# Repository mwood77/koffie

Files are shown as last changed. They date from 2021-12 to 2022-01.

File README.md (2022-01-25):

# Koffie ☕
Koffie is an open source project which allows you to programatically set and adjust the boiler pressure of your espresso machine in real time.

Too much reading? [Watch an overview of the device here!](https://www.youtube.com/watch?v=FLI8BKzOYMY)

### Current development (features requests and bugs)
You can find the task board here, which shows work in progress: 
- [View our project board](https://github.com/mwood77/koffie/projects/1)

### Found a bug?
- [Report it here - please make sure to include the what & how](https://github.com/mwood77/koffie/issues/new)

### Want to contribute? Great!
- Fork it and create a PR!

## Read first!
- This proceedure is 100% reversible
- There are some passive safety limitations built into the software, which include:
    - You have a maximum boiler pressure of 1.4 BAR
- This project was designed/developed on a pre-millenium La Pavoni Europiccola (double rocker; power switch + hi/low)
    - Your implementation may be different than what's documented here, but with some simple probing of your espresso machine circuitry, you should be able to implement this easily.

# User guide
> By default, koffie boots into espresso mode

## Automatic Mode
- Tap either button to toggle between programming modes:
    - Espresso (low pressure)
    - Milk (high pressure)
- The screen will update to show you what mode you're currently in, in addition to the LEDs (if equipped).

## Manual Mode
- Turning the rotary encoder (knob) will toggle Koffie into Manual mode.
    - The pressure readout will show a **Target (TARG:)** and **Actual (ACTL:)** values. 
    - Turning the encoder will either increase or decrease the **target value**. Koffie will then take action to intercept the target value.
- The screen will update to show you what mode you're currently in, in addition to the LEDs (if equipped).

## Programming Mode
In addition to Automatic and Manual operation, you may also overwrite the default pressure values in Koffie's memory. Do set custom values do the following:
1. Turn on Koffie (your espresso machine does not need to be on).
1. Turn the encoder to swtich into **Manual Mode**
1. Set the **Target (TARG:)** to your desired pressure level.
1. Press and hold either button until the LED flashes (approx. 2 seconds)
    - Your new value is now stored in memory.
1. Tap the same button to go back to automatic mode and check that value on screen is the value you saved. If not, repeat the steps above.

# Build and install your own Koffie
This section has been split across multiple pages to make the project easier to digest.
1. [Design document](docs/design.md) **<- START HERE**
1. [Parts list and costs](docs/requirements.md)
1. [Circuit diagrams](docs/circuits.md)
1. [Code Configurables](docs/code_configurables.md) **<- READ THIS BEFORE UPLOADING THE CODE TO YOUR ARDUINO**

### Installation (Machine specific)
- La Pavoni
    1. [Europiccola](docs/machines/europiccola.md)

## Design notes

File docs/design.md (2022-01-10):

> [Back to main page](../README.md)

# Design document
The purpose of this document is:
- To outline what functionality the PID, "koffie," has
- How "koffie" behaves when iteracted with by a human
- How "koffie" interacts with an espresso machine

## Program modes
1. Espresso - low pressure for extracting espresso
1. Milk - high pressure for frothing milk
1. Manual - "on the fly" pressure adjustment
1. Programming - overwrite the default pressure levels with custom values

## Controls
- 2 momentary buttons which are used to set and access stored values
    - Button 1:
        - **Momentary press:**
            1. deactivate current program
            1. activate "Espresso Mode" & call-up pressure for extracting espresso
        - **Long press:**
            - See [Progamming Mode](../README.md#programming-mode)
    - Button 2:
        - **Momentary press:** 
            1. deactivate current program
            1. activate "Milk Mode" & call-up pressure for frothing milk
        - **Long press:**
            - See [Progamming Mode](../README.md#programming-mode)
- 1 multi-function rotary encoder
    - If in Espresso or Milk modes:
        - deactivate current program
        - activate "Manual Mode," and enable on-the-fly boiler pressure adjustment
    
## GUI
### Block diagram of interface

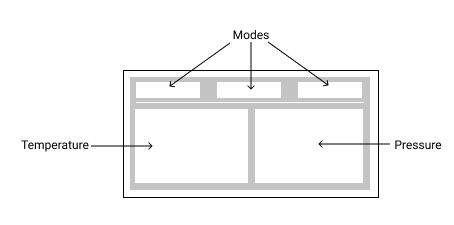
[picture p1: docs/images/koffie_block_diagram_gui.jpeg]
Block diagram of koffie interface


### Populated block diagram interface
|  |  |
| - | - |
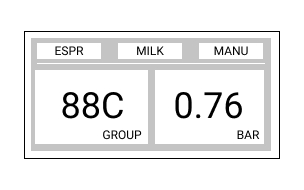
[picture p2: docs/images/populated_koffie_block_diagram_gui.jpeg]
Block diagram of koffie interface
|  | - A single mode is illuminated when activated <br/> - When in "programming mode," the corresponding parent mode will flash <br/> - Temperatures are displayed, if available <br/> - if no probe is connected, `N/C` is displayed |

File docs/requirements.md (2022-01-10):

> [Back to main page](../README.md)

# Parts list and costs

## How much will this cost?
That's hard to answer, but if you purchase everything in the list beneath, it should come to no more than **$60 USD / €53**. 

## Things I've assumed you already know and own
- A "dumb" espresso machine
- A computer
    - The tutorial is written using a Mac, but a Windows or Linux computer is also fine. The instructions should be interchangable.
- A spare phone charger & USB cable to power the Arduino
- How to use a multimeter
- How to solder and de-solder
- Some spare small-gauge wire
- Rudimentary knowledge of electronics
- Some understanding of code (C++) and/or how to use an Arduino
    - However if you follow the instruction to the letter, you should be able to get by without any previous experience.

## Required parts
> You requirements may differ, so this list may or may not be complete depending on what sensors you want to install / your espresso machine.

I've provided links to the parts where I can. Most are sourced from Aliexpress as that's usually the most cost effective option.

#### La Pavoni Europiccola & Professional
- [ ] [Arduino Nano or other compatible](https://aliexpress.com/item/4000903444456.html). 
    - I chose the option: `Type-C USB`
        - If you choose `Type-C USB` be careful of the driver requirements (plug and play on Mac and Linux. Windows, not guaranteed). **If you don't know what this means, select a mico-USB one instead.**
- [ ] [Arduino expansion board](https://s.click.aliexpress.com/e/_9RjuPG).
    - **This is optional**, but it reduces your soldering workload / allows you to wire in new sensors quickly.
- [ ] [A solid state relay](https://s.click.aliexpress.com/e/_9h01hI). 
    - Select the `SSR-40 DA` option, **or make sure you choose a solid state relay that can handle roughly 40A and mains voltage (100-240V).**
- [ ] [An OLED screen](https://nl.aliexpress.com/item/32957309383.html). 
    - An OLED screen has a very wide viewing angle, is high contrast, and is not complex to implement.
- [ ] [An encoder](https://s.click.aliexpress.com/e/_AZFjme). 
- [ ] [A knob for the encoder](https://s.click.aliexpress.com/e/_Atgtlq). 
    - The better the knob, the better the encoder will feel!
- [ ] [2x illuminated momentary switches](https://s.click.aliexpress.com/e/_AFDd3K). 
    - We will be using them to quick-select different memory modes ("Brew mode" & "Frothing mode").
        - Select: 
            - Color: `16 Ring LED`
            - Voltage: `3-6V`
            - Size: `Self-reset momentary`
            - Standard: `choose whatever LED colour you'd like. I'd recommend matching it to your OLED.`
            - Quantity: `2`
- [ ] [An enclosure to mount the electronics](https://s.click.aliexpress.com/e/_AKRz3E).
- [ ] [2x TMP36 analog temperature sensors](https://s.click.aliexpress.com/e/_AWMTHm).
    - We'll hack this to fit in the joint between the group head and boiler.
- [ ] [2x 4k7 resistors (also known as 4700 ohms or 4.7K resistors)](https://www.google.com/search?q=4k7+resistor).
    - We'll use these on our switch's LEDs.
- [ ] [2x A pressure transducer with a minimum rating of 30 PSI / 2 BAR.](https://s.click.aliexpress.com/e/_ALg5YG). 
    - I use 60PSI sensors in this project, but you can change this variable in the project code.
    - I'd recommend you buy 2 examples as these have a habit of failing.
    - This one is great, as the thread size (1/8 NPT) is compatible with the Europiccola's manometer adapter (the gauge adapter that screws atop the sight glass).
    - If you don't have an existing pressure gauge, or need an adapter for this project:
        - [M12 to 1/8 NPT adapter](https://www.google.com/search?q=europiccola+m12+to+1%2F8+npt)
        - [M11 to 1/8 NPT adapter](https://www.google.com/search?q=europiccola+m11+to+1%2F8+npt)
        - If you don't know what size to buy, remove the "big screw" on top of the sight glass and measure the diameter of the threads.
            - 11mm = M11 
            - 12mm = M12

### Optional Extras
- [ ] [Kapton Tape](https://www.google.com/search?q=kpaton+tape).
    - We'll use this to attach our sensors to the coffee machine (this is heat resistant tape).
- [ ] If you have access to a 3D printer, you can print off a faceplate for the enclosure I've linked above.
    - [Find the models here](https://github.com/mwood77/koffie/tree/main/models)

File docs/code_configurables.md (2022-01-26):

> [Back to main page](../README.md)

# Code configurables

## Prerequisites
If you've never used/programmed an Arduino before, I'd strongly suggest you start here:
1. [Arduino - Getting Started](https://www.arduino.cc/en/Guide)
1. [Arduino Nano Quickstart](https://docs.arduino.cc/hardware/nano)

There are a number of files but there are only a few things you **might** need to change. 
You can find these configurable values located between the following headers in `koffie.ino`

<hr>
Please read the comments closesly and do not change any of the other code unless you understand what is going on. If you can see an improvement point, please raise a PR!
<hr>

```
 File: ~/koffie/koffie.ino

// *************************************************************************************
// ****************************** BEGIN CONFIGURABLES **********************************
// *************************************************************************************
 
...
...
...

// *************************************************************************************
// ******************************* END CONFIGURABLES ***********************************
// *************************************************************************************
```

## Arduino Libraries Required
Most of the required libraries are included, or are automatically downloaded on the first compilation.

If the Arduino IDE (2.0) fails to compile the code, it's probably unable to find a library. Please make sure you've downloaded the following (slightly obscure) libraries:

1. **Encoder** - by Paul Stoffregen
    - Version 1.4.2
1. **OneButton** - by Matthias Hertel
    - Version 2.0.4
1. **Adafruit SSD1306** - by Adafruit
    - Version 2.5.1
    - Make sure to install all of the required dependencies

## Helpful hints
1. Make sure to turn on the option `Show verbose output during: [x] compile`
    - This is found under **Arduino IDE** -> **Preferences** on macOS
    - This is found under **File** -> **Preferences** on Windows
    - This will give a lot of output during compile, but it makes it much easier to diagnose what went wrong.

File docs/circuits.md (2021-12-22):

> [Back to main page](../README.md)

# Circuit diagrams

## Arduino
You can view an online version of the circuit diagram here:
- [Koffie - arduino wiring diagram](https://crcit.net/c/60b06504545248359b3b8e42acd408be)

Alternatively, you can view a visual representation of the wiring on the emulated version of this project:
 - [Koffie - running in an arduino simulator](https://wokwi.com/arduino/projects/316601625012601409)

### Circuit Diagram
wiring diagram for koffie

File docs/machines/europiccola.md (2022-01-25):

> [Back to main page](../../README.md)

# Europiccola

## Wiring
- Wire the relay's switched voltage (mains) between the thermocouple (thermal fuse) and the power switch.
- If your machine does not have a thermocouple, wire the relay between the switch.

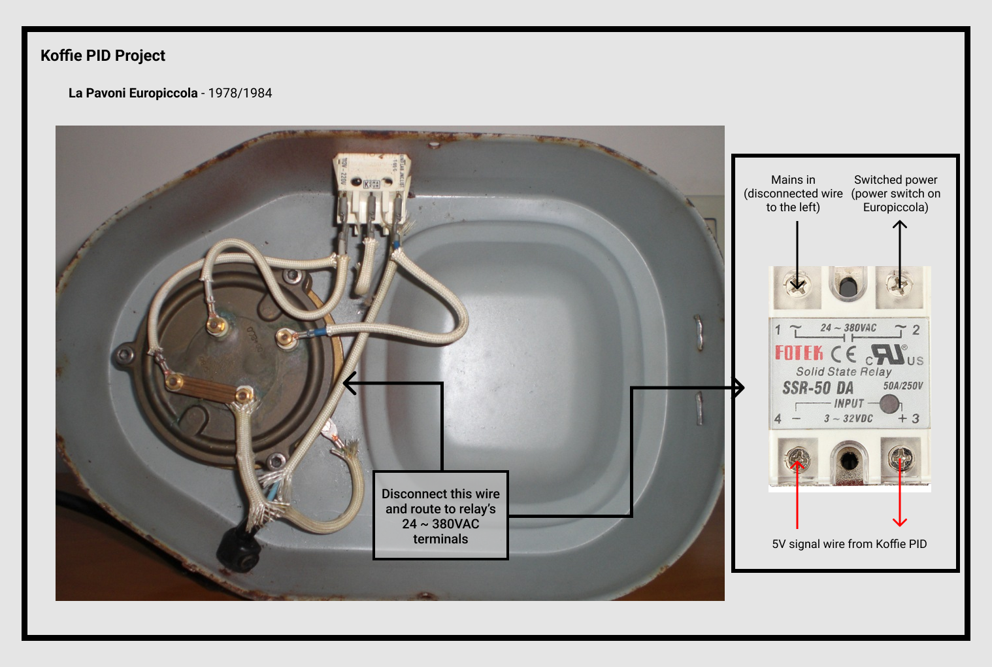
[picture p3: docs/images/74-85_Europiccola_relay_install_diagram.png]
image of europiccola ball bearing pressure safety valve
    
    - **Image Credit**: 
        - Francesco Ceccarelli
        - [La Pavoni - wiring diagrams](http://www.francescoceccarelli.eu/lapavoni_schemi_eng.htm)

## Modifying the pressure
> ⚠️ This is exceptionally dangerous! Only do so at your own risk! ⚠️

### Mechanical Pressure Valve
Should you want more pressure from your boiler, do the following:
- Dissasemble the mechanical pressure valve and slightly pull on the spring. By stretching it out, you increase the pressure placed on the ball bearing, which will increase the amount of pressure required to actuate the valve. This increases the overall boiler pressure.
- Make small adjustments, then bring the machine up to temperature and check at what pressure the valve opens. Re-adjust as necessary.
- **DO NOT TAKE THE PRESSURE ABOVE 1.5 BAR!** That is unsafe, and there is no need to brew espesso/froth milk at pressures above 1.3 BAR.
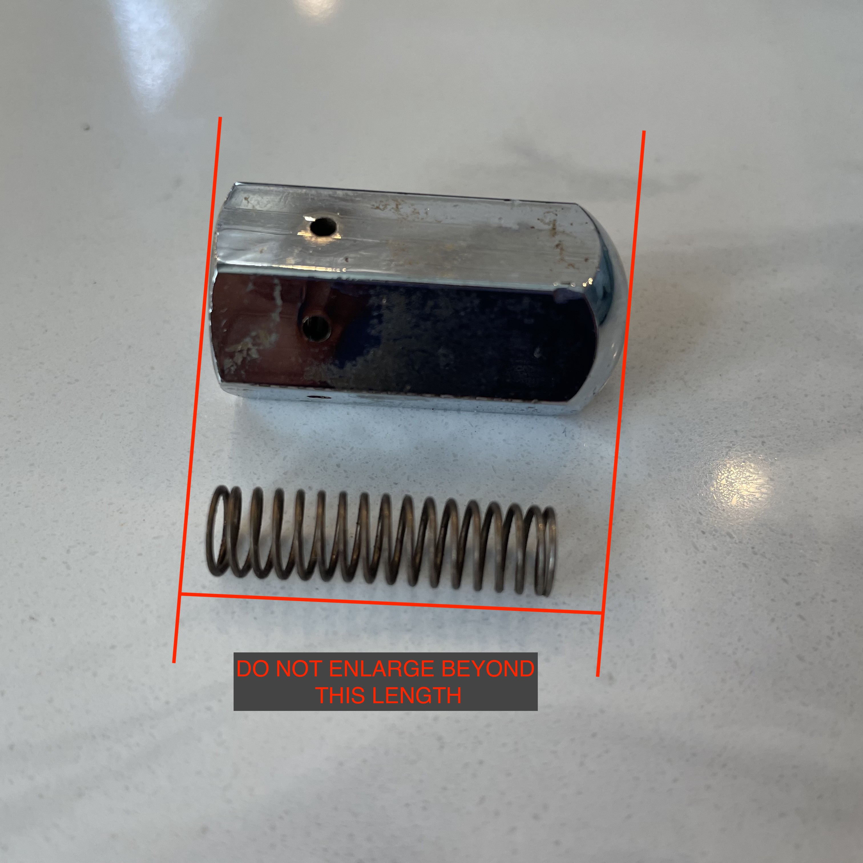
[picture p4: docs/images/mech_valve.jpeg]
image of europiccola ball bearing pressure safety valve
    
    - **Image Credit**: 
        - Robert McKeon Aloe
        - ["Increasing the Pressure for La Pavoni: Better Espresso"](https://towardsdatascience.com/increasing-the-pressure-for-la-pavoni-espresso-2a8ee0febb1e)

### Pressurestat Models
- https://www.google.com/search?q=europiccola+pressurestat+increase+pressure

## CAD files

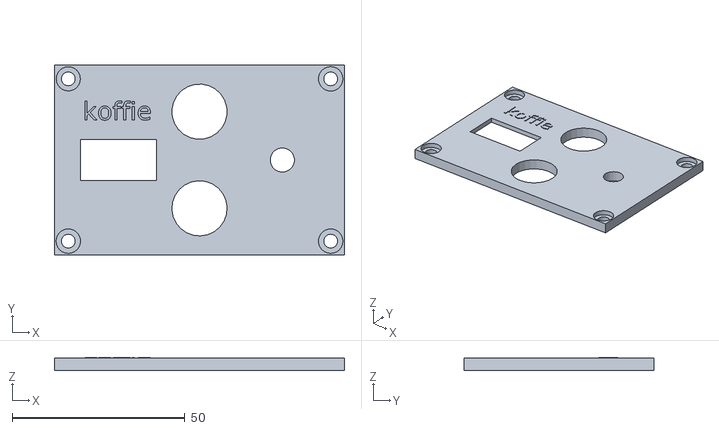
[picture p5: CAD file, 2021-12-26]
models/V1_koffie_faceplate.stl
84.0 x 55.0 x 3.81

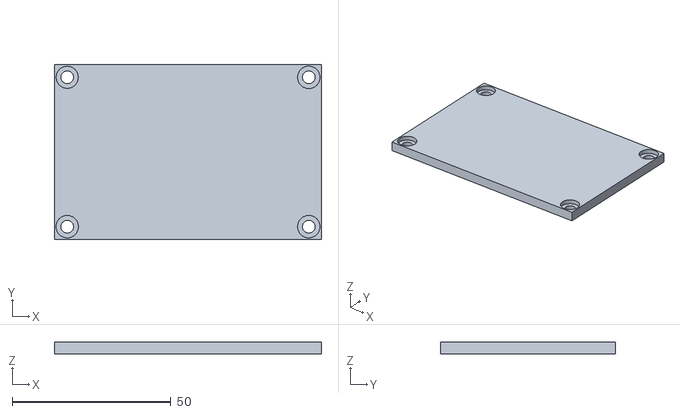
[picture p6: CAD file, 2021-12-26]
models/V1_koffie_blank_faceplate.stl
84.0 x 55.0 x 3.62

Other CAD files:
models/V1_koffie_faceplate.skp

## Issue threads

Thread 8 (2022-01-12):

Add safety guard against sensor errors

mwood77, 2022-01-12:
Pressure sensors are fragile and prone to throw trash data (get sorted easily). Programmatically guard against this by setting duty cycle to 0% if this goes above a certain threshold.

mwood77, 2022-01-15:
Current solution under test:

 1. On boot, set constant `INIT_TEMPERATURE` as group head's current temp.
 1. Compare previous pressure sensor input to current pressure sensor input (pressure in BAR)
 1. If value difference is greater than `2.0`, increment `ERROR_COUNT` (init @ 0).
 1. If `ERROR_COUNT` is greater than or equal to `20` && current group head temperature is greater than `INIT_TEMPERATURE + 10`, set fail condition and shut off relay (turn off power).

----------------------------

`INIT_TEMPERATURE + 10` is needed, as known good pressure sensors throw a large amount of unreliable data during initial power up/heating; it takes some time for the sensor to stabilize during the first 5 minutes of operation.

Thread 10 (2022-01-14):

Koffie vNext

mwood77, 2022-01-14:
This is a placeholder for the next major version of the project. It'll include new design ideas, considerations, and stretch goals.

Considerations:
- Wireless communication (ESP32?)
- Upgrade microcontroller to either Pi Pico or ESP32
- integrate larger screen

Stretch Goals
- Design with pressure profiling capabilities in mind

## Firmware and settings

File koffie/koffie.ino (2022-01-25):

  /*
  *
  *  
  * Welcome!
  * Author: Michael Wood
  * Date: 10 January, 2022
  *
  * You can find an emaulated "koffie" running here --> https://wokwi.com/arduino/projects/316601625012601409
  * There are some caveats for the emulator:
  *     - the temperature doesn't display right (tmp36 is not available)
  *     - there's no pressure sensor connected
  *     - there's no relay connected
  *
  *
  * LICENSE
  * 
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
  * THE SOFTWARE IS PROVIDED "AS IS", WITHOUT WARRANTY OF ANY KIND, EXPRESS OR
  * IMPLIED, INCLUDING BUT NOT LIMITED TO THE WARRANTIES OF MERCHANTABILITY,
  * FITNESS FOR A PARTICULAR PURPOSE AND NONINFRINGEMENT. IN NO EVENT SHALL THE
  * AUTHORS OR COPYRIGHT HOLDERS BE LIABLE FOR ANY CLAIM, DAMAGES OR OTHER
  * LIABILITY, WHETHER IN AN ACTION OF CONTRACT, TORT OR OTHERWISE, ARISING FROM,
  * OUT OF OR IN CONNECTION WITH THE SOFTWARE OR THE USE OR OTHER DEALINGS IN THE
  * SOFTWARE.
  */
  #include <SPI.h>
  #include <Wire.h>
  #include <EEPROM.h>
  #include <Encoder.h>
  #include <OneButton.h>
  #include <Adafruit_SSD1306.h>

  #include "Relay.h"
  #include "PID_v1.h"
  #include "Thread.h"

  /*
  * DO NOT CHANGE THESE VARIABLES!
  */
  unsigned int EEPROM_PRESSURE_ADDRESS{0};
  int TEMPERATURE_SMOOTHING_HOLDER_POSITION{0};
  int TEMPERATURE_SMOOTHING_HOLDER[5]{0, 0, 0, 0, 0};
  int CURRENT_MODE;
  bool PROGRAMMING_MODE = false;
  long OLD_ENCODER_POSITION{0};
  double const STEP_SIZE{0.02};
  double const UPPER_LIMIT{1.4};                              // UPPER LIMIT IN BAR
  double const LOWER_LIMIT{0.0};
  long const THREAD_INTERVAL{1000};
  int const RELAY_CONTROL_DURATION{1};                        // 1 = 1 second
  double MEASUREMENT_INPUT;                                   // declare and initialize PID variables
  double CONTROL_OUTPUT;                                      // declare and initialize PID variables
  double SETPOINT;                                            // declare and initialize PID variables

  /*
  * Data Model
  */
  struct PRESSURE_SETTINGS {
    float espresso;
    float milk;
  };

  /*
  * Default pressure values in BAR
  */
  static PRESSURE_SETTINGS defaultPressures = {
    0.74f, 
    1.10f
  };

  /*
  * Instantiate object for user's programmable temperature values
  */
  PRESSURE_SETTINGS usersDesiredTemperatures;

  // *************************************************************************************
  // ****************************** BEGIN CONFIGURABLES **********************************
  // *************************************************************************************
  /*
  * PRESSURE_SENSOR_INPUT_PIN = Set which DIGITIAL pin your PRESSURE probe's signal wire is connected to.
  * RELAY_CONTROL_OUTPUT_PIN = Set which DIGITIAL pin your RELAY's signal wire is connected to.
  * PRESSURE_TRANSDUCER_MAX_PSI = Set the maximum pressure your pressure sensor can read (EX -> if you bought a 30 PSI sensor, this value is 30.0)
  * ATMOSPHERIC_OFFSET = Set the pressure offset of your sensor. 
  *     To get this value, upload the code to your arduino and run it with the serial monitor open and with your pressure sensor attached. 
  *     If the "MEASUREMENT_INPUT" is "0.0" then use 0.0 as the value.
  *     If the reading is anything else (EX -> "MEASUREMENT_INPUT: -0.10"), then enter 0.10
  *
  * These values are critical for the relay control
  */
  float const PRESSURE_SENSOR_INPUT_PIN{A3};
  double const RELAY_CONTROL_OUTPUT_PIN{11};       // PWM compatible output @ 498 Hz (CHECK BEFORE CHANGING)
  const int PRESSURE_TRANSDUCER_MAX_PSI = 60.0;    // Change this value to the maximum value your pressure sensor can read in PSI. Ex: 30 PSI sensor = 30.0
  const double ATMOSPHERIC_OFFSET{0.0};            // Example offset of -0.17 (measured against physical gauge)

  /*
  * These values control the overall "tuning" of the PID. 
  * I'd strongly recomment NOT changing these, but if you find the tune needs adjusting, use this resource: 
  *   - https://robotics.stackexchange.com/questions/167/what-are-good-strategies-for-tuning-pid-loops
  */  
  double KP{20};                    // PID constant = P value
  double KI{10};                    // PID constant = I value
  double KD{18};                    // PID constant = D value

  /*
  * Used when converting the temperture probes output voltage to milivolts.
  * 5.0 = 5V input
  * 3.3 = 3.3V input
  */
  double const PIN_VOLTAGE{5.0};

  /*
  * Set which ANALOGUE pins your TEMPERATURE probe's signal wire(s) are connected to
  * 
  * https://learn.adafruit.com/tmp36-temperature-sensor/using-a-temp-sensor
  */
  int const GROUP_TEMP_PIN{A2};

  /*
  * Set which unit of measure you want to display.
  * Options are:
  *     - 'C'   (temperature in C and pressure in BAR)
  *     - 'F'   (temperature in F and pressure in PSI)
  *     - 'K'   (temperature in K and pressure in BAR)
  */
  char const MEASUREMENT_UNIT{'C'};

  /*
  * A0 = to the pin your switch is wired to, set it to whatever ANALOG pin you've wired your switch into
  * MILK_LED{6} = the positive side of your LED, set "6" to the pin your LED is wired to
  */
  OneButton buttonMilk(A0, true);
  int const MILK_LED{6};

  /*
  * A1 = to the pin your switch is wired to, set it to whatever ANALOG pin you've wired your switch into
  * ESPRESSO_LED{7} = the positive side of your LED, set "7" to the pin your LED is wired to
  */
  OneButton buttonEspresso(A1, true);
  int const ESPRESSO_LED{7};

  /*
  * 2 = the DT pin of your encoder - Set this value to whatever DIGITAL pin you've used on your Arduino
  * 3 = the CLK pin ofyour encoder - Set this value to whatever DIGITAL pin you've used on your Arduino
  */
  Encoder encoder(3, 2);

  /*
  * Set the screen width and height here. If you bought the OLED listed in the documentation, there's no need
  * to change anything. 
  */
  int const SCREEN_WIDTH{128};        // OLED display width, in pixels
  int const SCREEN_HEIGHT{64};        // OLED display height, in pixels
  int const OLED_RESET{-1};            // Reset pin 
  // *************************************************************************************
  // ******************************* END CONFIGURABLES ***********************************
  // *************************************************************************************

  Thread timerThread = Thread();
  Adafruit_SSD1306 display(SCREEN_WIDTH, SCREEN_HEIGHT, &Wire, OLED_RESET);
  PID pidControl(&MEASUREMENT_INPUT, &CONTROL_OUTPUT, &SETPOINT, KP, KI, KD, DIRECT);
  Relay relay(RELAY_CONTROL_OUTPUT_PIN, RELAY_CONTROL_DURATION);

  void setup() {

    Serial.begin(9600);
    display.begin(SSD1306_SWITCHCAPVCC, 0x3C);
    pinMode(MILK_LED, OUTPUT);
    pinMode(ESPRESSO_LED, OUTPUT);
    pinMode(RELAY_CONTROL_OUTPUT_PIN, OUTPUT);
    pinMode(LED_BUILTIN, OUTPUT);

    buttonMilk.attachClick(handleClickMilk);
    buttonMilk.attachLongPressStart(saveProgramMilk);
    
    buttonEspresso.attachClick(handleClickEspresso);
    buttonEspresso.attachLongPressStart(saveProgramEspresso);

    timerThread.onRun(updateTemps);
    timerThread.setInterval(THREAD_INTERVAL);

    checkEepromState();

    relay.setRelayMode(relayModeAutomatic);
    pidControl.SetMode(AUTOMATIC);
    
    initialize();                                             // initializes state as "espresso" & does user feedback setup

  }

  void loop() {
    buttonMilk.tick();
    buttonEspresso.tick();
    handleEncoder();
    delay(100);

    if (timerThread.shouldRun()) {
      timerThread.run();
    }
    
  }

  /**
  * Checks if save-state exists in memory & writes to it if it doesn't
  */
  static void checkEepromState() {
    PRESSURE_SETTINGS result;

    if (EEPROM.read(EEPROM_PRESSURE_ADDRESS) == 255) {
      EEPROM.put(EEPROM_PRESSURE_ADDRESS, defaultPressures);
    } 
    result = EEPROM.get(EEPROM_PRESSURE_ADDRESS, result);
    usersDesiredTemperatures = result;
  
  }

  /**
  * Saves new default values to EEPROM
  * @param mode integer - the program mode to modify (*ex. Milk)
  * @param setpoint float - the setpoint value to save to memory
  */
  static void setEepromState(int mode, float setpoint) {
    PRESSURE_SETTINGS state;
    state = EEPROM.get(EEPROM_PRESSURE_ADDRESS, state);

    if (mode == 6) {
      usersDesiredTemperatures.milk = setpoint;
    }
    if (mode == 7) {
      usersDesiredTemperatures.espresso = setpoint;
    }

    if (state.espresso != usersDesiredTemperatures.espresso || state.milk != usersDesiredTemperatures.milk) {
      EEPROM.put(EEPROM_PRESSURE_ADDRESS, usersDesiredTemperatures);
    }
    
  }

  /**
  * Handles encoder functionality if movement detected
  */
  static void handleEncoder() {
    int const manualMode{25};
    long newEncoderPosition = encoder.read();

    if (newEncoderPosition != OLD_ENCODER_POSITION) {
      if ( CURRENT_MODE != manualMode ) {
        CURRENT_MODE = manualMode;
        drawActiveMode(CURRENT_MODE);

        if (checkStateLED(ESPRESSO_LED) == HIGH) {
          toggleLED(ESPRESSO_LED);
        }

        if (checkStateLED(MILK_LED) == HIGH) {
          toggleLED(MILK_LED);
        }
      }

    if (OLD_ENCODER_POSITION < newEncoderPosition) {          // rotating clockwise
          SETPOINT += STEP_SIZE;

          if (SETPOINT > UPPER_LIMIT) {
            SETPOINT = UPPER_LIMIT;
          }

      } else {
        SETPOINT -= STEP_SIZE;

        if (SETPOINT < LOWER_LIMIT) {
          SETPOINT = LOWER_LIMIT;
        }
        
      }

      OLD_ENCODER_POSITION = newEncoderPosition;
    }

  }

  /**
  * RED BUTTON IN EMULATOR
  *
  * Handles buttons functionality for Milk
  */
  static void handleClickMilk() {

    if (checkStateLED(ESPRESSO_LED) == HIGH) {
      toggleLED(ESPRESSO_LED);
    }

    CURRENT_MODE = MILK_LED;
    SETPOINT = usersDesiredTemperatures.milk;

    if (checkStateLED(MILK_LED) == LOW) {
      toggleLED(MILK_LED);
    }

    drawActiveMode(CURRENT_MODE);
    
  }

  /**
  * BLUE BUTTON IN EMULATOR
  *
  * Handles buttons functionality for Espresso
  */
  static void handleClickEspresso() {

    if (checkStateLED(MILK_LED) == HIGH) {
      toggleLED(MILK_LED);
    }

    CURRENT_MODE = ESPRESSO_LED;
    SETPOINT = usersDesiredTemperatures.espresso;

    if (checkStateLED(ESPRESSO_LED) == LOW) {
      toggleLED(ESPRESSO_LED);
    }
  
    drawActiveMode(CURRENT_MODE);

  }

  /**
  * Saves new programming value for espresso
  */
  static void saveProgramEspresso() {
    setEepromState(7, SETPOINT);
    blinkLED(7);

  }

  /**
  * Saves new programming value for milk
  */
  static void saveProgramMilk() {
    setEepromState(6, SETPOINT);
    blinkLED(6);

  }

  /**
  * Rapidly blinks the LED 
  */
  static void blinkLED(int mode) {
    for (int i = 0; i < 6; i++) {
      toggleLED(mode);
      delay(200);
    } 

  }

  /**
  * Configures operation mode and static gui elements
  */
  static void initialize() {
    CURRENT_MODE = ESPRESSO_LED;
    toggleLED(ESPRESSO_LED);
    
    SETPOINT = usersDesiredTemperatures.espresso;
    
    initializeDisplay();

  }

  /**
  * Clears the display then begins the screen initilization
  */
  static void initializeDisplay() {
    display.clearDisplay();
    drawStaticGUI();

  }

  /**
  * Changes the continuous ON of OFF state of an LED
  *
  * @param pin integer - the LED's pin number to toggle ON or OFF.
  */
  static void toggleLED(int pin) {
    const boolean state = digitalRead(pin);
    digitalWrite(pin, !state);

  }

  /**
  * Returns the current byte state (HIGH or LOW) of an LED's pin.
  *
  * @param pin integer - the LED's pin number to check.
  * @return the byte code of the given LED's state (HIGH or LOW)
  */
  static byte checkStateLED(int pin) {
    return digitalRead(pin);

  }

  /**
  * Averages the total value of an array (ex. pressure or temp) and returns a single value
  *
  * @param array int[5] - the array[5] with values to average
  * @return the averaged result of arrayToSmooth
  */
  static float smoothValues(int *array) {
    float sum;

    for (int i = 1; i <= 5; i++) {
      sum += array[i];
    }

    sum /= 5;
    return sum;

  }

  /**
  * Measures the temperature of attached temperature probes.
  * Also blinks current mode's LED if PROGRAMMING_MODE = TRUE
  */
  static void updateTemps() {
    digitalWrite(LED_BUILTIN, HIGH); 
    int const group = analogRead(GROUP_TEMP_PIN);
    float const groupTemperature = convertTemperatureUnits(group);
    int const numberOfSmoothedElements = sizeof(TEMPERATURE_SMOOTHING_HOLDER)/sizeof(TEMPERATURE_SMOOTHING_HOLDER[0]);

    if (TEMPERATURE_SMOOTHING_HOLDER_POSITION > numberOfSmoothedElements) {
      TEMPERATURE_SMOOTHING_HOLDER_POSITION = 0;
    } else {
      TEMPERATURE_SMOOTHING_HOLDER[TEMPERATURE_SMOOTHING_HOLDER_POSITION] = groupTemperature;
      TEMPERATURE_SMOOTHING_HOLDER_POSITION++;
    }

    drawTemperatures(smoothValues(TEMPERATURE_SMOOTHING_HOLDER));
    updatePressure();

    if (PROGRAMMING_MODE == 1) {
      toggleLED(CURRENT_MODE);
      drawActiveMode(CURRENT_MODE);
    }

    digitalWrite(LED_BUILTIN, LOW); 

  }

  /**
  * Measures the pressure of attached pressure probe and updates PID values
  */
  static void updatePressure() {
    float dutyCycle = relay.getDutyCyclePercent();
    float sensor = analogRead(PRESSURE_SENSOR_INPUT_PIN);
    float convertedReading = convertPressureUnits(sensor);

    MEASUREMENT_INPUT = convertedReading;

    if (MEASUREMENT_INPUT > SETPOINT) {
      relay.setDutyCyclePercent(0);
      relay.setRelayPosition(relayPositionOpen);                // change relayPositionOpen to relayPositionClosed if your relay is normally open
    } else {
      relay.setDutyCyclePercent(CONTROL_OUTPUT / 255.0);        // Relay library only accepts values between 0 and 1
    }

    // COMPUTE PID LEVELS
    pidControl.Compute();
    
    // APPLY PID COMPUTE TO RELAY
    relay.loop();

    // Serial.print(F("SETPOINT: "));
    // Serial.print(SETPOINT);                                   // only displays in BAR in serial monitor
    // Serial.print(F("  |  MEASUREMENT_INPUT: "));
    // Serial.print(MEASUREMENT_INPUT);
    // Serial.print(F("  |  dutyCycle: "));
    // Serial.print(dutyCycle * 100);
    // Serial.println(F("%"));

    drawPressure(convertedReading, PROGRAMMING_MODE);

  }

  /**
  * Converts milivolts to celcius, fahrenheit, or kelvin
  *
  * @param mv integer - milivolts measured from the temperature sensor
  * @return float - the value converted to the desired units
  */
  static float convertTemperatureUnits(int mV) {

    float voltage = mV * 5.0;
    voltage /= 1024.0;

    float celsius = (voltage - 0.5) * 100;
    float fahrenheit = (celsius * 9.0 / 5.0) + 32.0;

    switch(MEASUREMENT_UNIT) {
      case 'C':
        return celsius;
        break;
      case 'F':
        return fahrenheit;
        break;
      case 'K':
        return celsius + 273.15;
        break;
    }

  }

  /**
  * Converts voltage to BAR or PSI
  *
  * @param voltage float - milivolts measurement from the pressure sensor
  * @return float - the value converted to the desired units
  */
  static float convertPressureUnits(float voltage) {

    /*
    * y = mx + b
    * 
    * Credit to Oven's Garage for the formula beneath.
    * See it explained here: https://www.youtube.com/watch?v=UrqPxwsPWGk
    */
    const int pressureZero = 102.4;                           // analog reading of pressure transducer at 0 PSI - if you bought it from the guide, don't change.
    const int pressureMax = 921.6;                            // analog reading of pressure transducer at 60 PSI - if you bought it from the guide, don't change.

    const float result = ((voltage - pressureZero) * PRESSURE_TRANSDUCER_MAX_PSI) / (pressureMax - pressureZero);   // Result is in PSI
    float const PSI = result + ATMOSPHERIC_OFFSET;
    float const BAR = (result / 14.504) + ATMOSPHERIC_OFFSET;

    switch(MEASUREMENT_UNIT) {
      case 'C':
        return BAR;
        break;
      case 'F':
        return PSI;
        break;
      case 'K':
        return BAR;
        break;
    }

  }

  /**
  * Draws all static elements of the GUI
  */
  static void drawStaticGUI() {
    display.clearDisplay();

    display.setTextSize(1);
    display.setTextColor(WHITE);
    
    display.drawLine(0, 19, display.width(), 19, WHITE);
    display.drawLine(64, 19, 64, display.height(), WHITE);

    display.setCursor(30, 54);
    display.println(F("GROUP"));

    drawActiveMode(CURRENT_MODE);

  }

  /**
  * Draws temperature values on screen - called in protothread
  *
  * @param groupTemp integer - the converted value measured from the temperature sensor
  */
  static void drawTemperatures(int groupTemp) {
    display.fillRect(8, 25, 50, 25, BLACK);                   // Clear modes area
    display.setTextColor(WHITE, BLACK);                       // Prepare for overwriting data
    
    display.setTextSize(2);
    display.setCursor(8, 35);
    display.print(groupTemp);
    display.print(MEASUREMENT_UNIT);
    display.setTextSize(1);

  }

  /**
  * Draws pressure values on screen - called in protothread
  *
  * @param pressure float - pressure in units (not mV)
  * @param programmingMode integer - takes global variable PROGRAMMING_MODE
  */
  static void drawPressure(double pressure, int programmingMode) {
    double convertedSetPoint{0};
    convertedSetPoint = SETPOINT * 14.504;                    // Convert target display pressure from BAR to PSI 

    display.fillRect(66, 20, 62, 64, BLACK);
    display.setTextColor(WHITE, BLACK);

  
      // *********************************************************************************************************
      //  If you want to display a digital readout of the current (unfiltered) pressure in MANU mode,
      //  uncomment the lines beneath and the closing bracket at line 629.
      // *********************************************************************************************************
      //
      // if (CURRENT_MODE == 25) {
      //   display.setCursor(70, 28);
      //   display.print(F("TARG "));
      //   if (MEASUREMENT_UNIT == 'F') {
      //     display.print(convertedSetPoint);
      //   } else {
      //     display.print(SETPOINT);
      //   }
      //   display.setCursor(70, 48);
      //   display.print(F("ACTL "));
      //   display.print(pressure, 2);
      // } else {

      display.setTextSize(2);
      display.setCursor(74, 35);

      if (MEASUREMENT_UNIT == 'F') {
        display.print(convertedSetPoint);
      } else {
        display.print(SETPOINT);
      }

      display.setTextSize(1);
      display.setCursor(103, 54);

      if (MEASUREMENT_UNIT == 'F') {
        display.print(F("PSI"));
      } else {
        display.print(F("BAR"));
      }
    
    // }
    
    display.display();
  }

  /**
  * Draws current mode as a filled-in rectangle
  */
  static void drawModes() {
    display.fillRect(0, 0, 128, 14, BLACK);                   // Clear modes area
    display.drawRoundRect(2, 2, 40, 14, 4, WHITE);
    display.drawRoundRect(44, 2, 40, 14, 4, WHITE);
    display.drawRoundRect(86, 2, 40, 14, 4, WHITE);

    display.setTextColor(WHITE);

    display.setCursor(10, 6);
    display.println(F("ESPR"));
    display.setCursor(52, 6);
    display.println(F("MILK"));
    display.setCursor(94, 6);
    display.println(F("MANU"));

  }

  /**
  * Draws current mode as a filled rectangle
  *
  * @param activeMode integer - the number which represents the current mode in use: 6, 7, 25
  */
  static void drawActiveMode(int activeMode) {
    drawModes();
    display.setTextColor(BLACK);

    switch(activeMode) {
      case 6:
        display.fillRoundRect(44, 2, 40, 14, 4, WHITE);
        display.setCursor(52, 6);
        display.println(F("MILK"));
        break;
      case 7:
        display.fillRoundRect(2, 2, 40, 14, 4, WHITE);
        display.setCursor(10, 6);
        display.println(F("ESPR"));
        break;
      case 25:
        display.fillRoundRect(86, 2, 40, 14, 4, WHITE);
        display.setCursor(94, 6);
        display.println(F("MANU"));
        break;
    }
    
    display.setTextColor(WHITE);

  }

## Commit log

2021-11-29 code: added basic code to handle button states
2021-11-29 code: added basic encoder & refactored logging
2021-11-29 bug: fixed serial message not displaying
    [koffie.ino]
2021-11-29 code: added temperature conversion switch
2021-11-29 code: added prototreading and moved temperature reading to thread
2021-11-29 code: moved LED blinking logic to temperature thread, as was causing unwanted blocking behaviour.
2021-11-29 code: add gui wireframe
2021-11-30 code: added live temperature gui update to protothread & refactored comments
2021-12-01 code: added encoder mode switch
2021-12-01 code: tweaked encoder manual mode behaviour
2021-12-01 code: moved pressure drawing into separate method
2021-12-01 bug: fixed temperature overwrite
    [koffie.ino]
2021-12-03 feat(eeprom): added temp object save logic + added manual pressure target/actual GUI elements
2021-12-03 reanmed folder struct for arduino ide
2021-12-03 refactored due to memory errors when running on actual hardware
    [koffie.ino]
2021-12-04 2nd refactor due to power demand issues; branch from here
    [koffie.ino]
2021-12-04 add thread dependencies
2021-12-05 add PID dependency
2021-12-05 feature(PID): initialize PID controls
2021-12-05 feature(PID): clarified comments and added PID control limits
2021-12-06 refactored temperature to TMP36 usage + updated docs
2021-12-07 added basic PID control & connected to buttons
2021-12-07 refactored temperature calc function
2021-12-19 added linear voltage to psi equation
2021-12-19 changed pressure pin to analogue A3 + refactored UI to 1 temperature probe - GROUP
2021-12-19 refactor pressure equation
2021-12-20 updated display to reflect real-time pressure in PSI if display is set to 'F'
2021-12-22 refactored documentation - added circuit diagram, cleaned parts list, tidied code explanation
2021-12-26 added faceplate STL and model files
    [V1_koffie_blank_faceplate.stl, V1_koffie_faceplate.skp, V1_koffie_faceplate.stl]
2022-01-09 fixed PID control
2022-01-09 refined PID tuning
2022-01-10 tweaked PID constants + altered programing behaviour
2022-01-13 Update README.md
    added links to bug reporting & project board
2022-01-14 (fix): ticket #7 - added smoothing functionality to temperature probe & corrected bugged that caused reading to be too high
    [koffie.ino]
2022-01-25 chore(memory): clarified some comments, moved relay/pid compute() call to a different location

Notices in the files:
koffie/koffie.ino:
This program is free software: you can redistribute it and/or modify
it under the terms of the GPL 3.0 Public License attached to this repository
